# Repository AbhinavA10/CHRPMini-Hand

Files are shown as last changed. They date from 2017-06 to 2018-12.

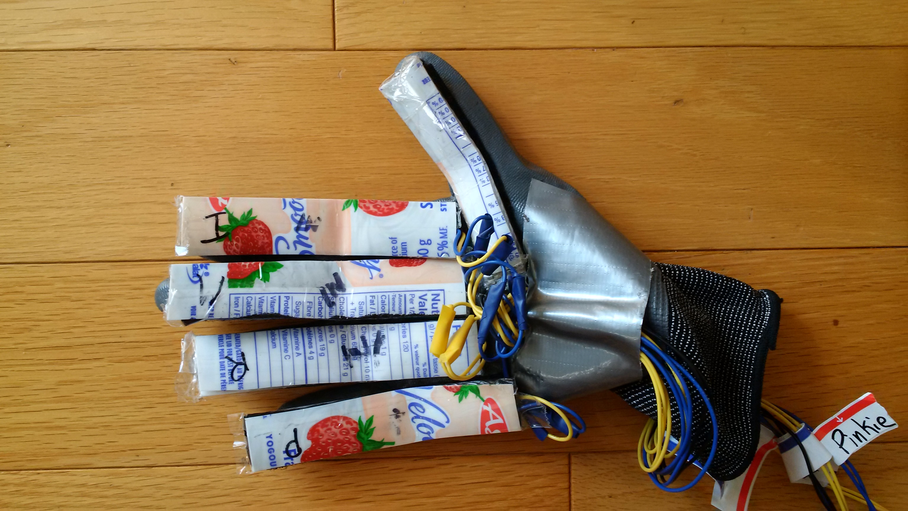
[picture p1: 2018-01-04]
images/Glove.jpg

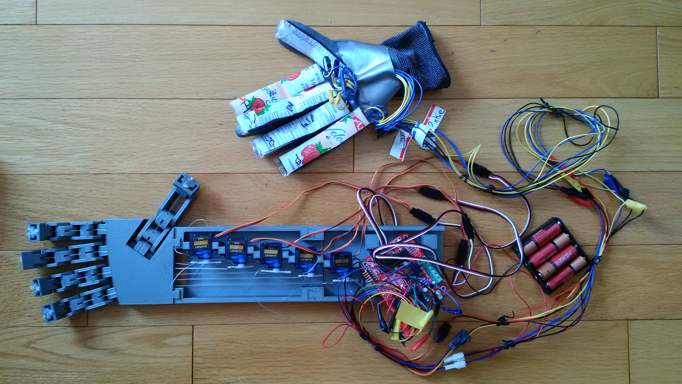
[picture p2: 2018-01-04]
images/Total.jpg

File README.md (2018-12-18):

# CHRPMini-Hand

This is the repo for a flex-controlled 3D printed robotic hand that I made as my summative, in grade 11 for Computer Engineering.
The technical report of this project can be found [here](docs/Technical_Report.pdf)

Demonstrations of the hand are available [here](videos)
Images of the hand can be found [here](images)

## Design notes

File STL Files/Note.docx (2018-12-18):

Measurements / Designs are in millimeters.

Base → Base of the finger (proximal phalanx)

Middle → Middle of the finger (intermediate phalanx)

Top → last joint of the finger (distal phalanx)

Cover → end part of the distal phalanx (fingertip)

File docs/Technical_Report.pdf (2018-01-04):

# Servo Controlled Robotic Hand with Flex Sensing

## Abhi Agrahari and Eric Schilla

## June 21

## Abstract

The main goal was to create an animatronic controller for a robotic hand. The user is to wear a glove, that has flex sensors attached (similar to the Nintendo Power Glove). These sensors’ values are processed by the board, and sent to the respective servos in the robotic hand. If the user bends their hand slightly, the robotic hand bends slightly. Thus, the robotic hand mimics the movement of the user’s hand.

## Table of Contents

Abstract
Table | of | Contents
Introduction
Hardware Design
Prototype Versioning of a Finger Palm and Arm Design
Flex Sensors
Software
Servo Timing
Github and MPLAB
Summary
Future Improvements
References
Appendix
GitHub Links:
Graphite-based Flex Sensor Technical Drawings of the Hand Basic Design
Fishing Line Paths
Screw Hole and Servo Dimensions Versions of the Index Finger
Original Design
Version 1 - Fundamental Design Flaw Version 2 and 3 - Joints are too loose Version 4 - Final Version, A Success

## Introduction

Any intermediate programmer that is experienced with hardware, like ourselves, would be able to understand this report. The general technologies involved are servos, and flex sensors.
For our summative, we wanted to create something that combined mechanical/hardware aspects, and programming/software aspects. On YouTube, we had seen videos of creating drones, and others of robotic body parts. After making a drone, we would feel like we have achieved quite a lot as we would have made something that can fly. However, the cost of making a drone would be much greater than buying one, and the store bought one would be better calibrated and suitable for flying. So there really was no point to that. When deciding on a robotic body part, we narrowed down to a couple. We chose to go with a hand because we could print and test many parts to create the needed joints, but also because we could find a way to make it mimic our movements. So overall, design and programming a robotic hand seemed like a good challenge for us.
This report intends to cover the design process behind both the mechanical aspects of the robotic hand, the self-made flex sensors, and the code created for this project.

## Hardware Design

For this project, we designed all hardware related components besides the servos, and the main circuit board. Essentially, we designed the flex sensors that are used, and the 3D printed hand. The 3D printed hand’s joints are controlled by fishing line, and are attached to 5x 9 gram micro servos.

## Prototype Versioning of a Finger

A long amount of time was spent in understanding and resolving the design to be able to have a finger that moves by pulling on two strings. Images of both prototype versions, and final versions can be seen in the appendix.
The versions progressed from not being able to move a finger at all due to a fundamental design flaw, to being able to fully bend all joints. A main difficulty was creating these joints to properly fit into one another. In the end, once a working version was made, we left the joints detachable instead of hooking onto one another as it is easier to create and assemble (see appendix for design).

## Palm and Arm Design

Besides having 5 similar fingers, we needed to also create a palm and an arm that the fingers would attach to. The palm was designed such that each finger’s fishing line had a unique path through the inside of the palm. This ensured that the lines did not cross over or tangle in each other. The arm’s servo supports were then aligned with the holes in the base of the palm so that enough torque could be generated by the 9 gram servos.

## Flex Sensors

Flex sensors are a special type of variable resistor. Their resistance changes as they bend. One side of the sensor is printed with a polymer ink that has conductive particles embedded in it. When the sensor is straight, the particles give the ink a low resistance, and when the sensor is bent away from the ink, the conductive particles move further apart, increasing this resistance. Thus, by combining the flex sensor with a static resistor we could create a voltage divider.
Or at least that was our idea. Originally, a plan was made to purchase 5-7 flex sensors from an online site, and use them. Unfortunately, flex sensors cost much too much (around $7) per sensor, so having just 5 sensors would have cost us around $35.
Various designs were found online to make these flex sensors. The designs had a general theme of using conductive foam, graphite covered paper, conductive thread and neoprene, and velostat. Purchasing conductive foam or velostat would have been very troublesome as no seller ships to Canada. So, many attempts were made to make flex sensors out of paper.
The design was sandwiching a piece of paper coloured with graphite, between two pieces of aluminum-taped cardboard. As expected, these did not work very well. Each sensor had large variations in the resistance it gave (~5kΩ), and each sensor by itself did not give consistent results.
Our next design was to sandwich conductive foam instead of paper. This worked much better, and all sensors give a reading of unbent → above 2.2kΩ and fully bent → below 300Ω. We then changed the sandwiching material to strips of yogurt boxes (plastic) instead of cardboard, so that the foam is bent more evenly, allowing greater sensitivity.
To create a voltage divider in this scenario that would give the maximum range for an input signal, we needed a static resistor of the average of 300Ω and 2.2kΩ. This would be a 1.25kΩ resistor. Fortunately, we had access to a 1.37kΩ resistor, which is close enough for our purposes.
Since we used the CHRPMini board, we created the voltage dividers by connecting the 1.37kΩ resistor to each PORTA 5V and PORTA signal pins. The flex sensor was then connected to the signal and the ground pin.

## Software

## Servo Timing

One thing we learned, is that each type of servo has a different timing. For example, the specifications sheet states that a 1ms pulse is -90°, and a 2ms pulse is +90°. However, after some trial and error, it was found that a 540µs pulse is -90°, and a 2.2ms pulse is +90°.

It was pointed out that Servo code isn’t necessarily exact, and can be fudged around a bit. However, we wanted to use the closest possible values. As such, in our code, we do some math to find the value to delay by so that the servos are pulsed every 20ms (see Hand.C in the CHRPMini-Hand repository on Github).

## Github and MPLAB

Getting github to work with MPLAB was difficult at some stages. We were not aware of how to properly integrate the two. Links to our githubs are available in the appendix.

## Summary

Overall, this project was very successful. The 9 gram micro servos were able to create enough torque and pull the fingers closed, and open them again, continuously. The conductive foam flex sensors also had enough variation in the resistance that the servos were able to move to different positions depending on the extremity of the bend. It is astounding that one is able to make flex sensors that cost at least $8, out of some conductive foam that is lying around from other products.
Some ideas this hand could be scaled to create are prosthetics, or a robotic extension for hazardous situations where having a human is not ideal.

## Future Improvements

A recommendation for the future is to buy flex sensors instead of making them ourselves. This would allow us to get more reliable and consistent results. Although making our own sensors using conductive foam was undoubtedly cool, buying them would also bring a greater level of professionalism.
Another future improvement is one that is software related. Currently the thumb is known as “zero” and the pinkie as “four”. We could write code to map finger numbers to more natural values (e.g., Thumb is “one” and Pinkie is “five”). Another code improvement would be to calibrate the flex sensors. This is currently a work in progress. The best way to do it would be to have a 10 second startup period where the user flexes the sensors repeatedly. The program would then determine the lowest resistance/value that each individual flex sensor has. That value would then be mapped to position 255 on the servo. This way, each flex sensor is able to fully bend it’s respective robotic hand piece, regardless of the slight difference in sensors.

## References

Below are websites and pdfs that we referenced while creating this project.

PIC18F25K50 Datasheet (http://ww1.microchip.com/downloads/en/DeviceDoc/30684A.pdf)
SG90 9gram MicroServo Datasheet (http://www.micropik.com/PDF/SG90Servo.pdf)
Learning Fusion 360 (http://help.autodesk.com/view/fusion360/ENU/)
About Flex sensors (https://learn.sparkfun.com/tutorials/flex-sensor-hookup-guide)
Paper Flex Sensors (https://www.youtube.com/watch?v=b7zT94WV-Ek)
Determining Size of array in C (https://stackoverflow.com/questions/37538/how-do-i-determine-the-size-of-my-array-in-c)

## Appendix

## GitHub Links:

https://github.com/AbhinavA10https://github.com/EricSchilha

## Graphite-based Flex Sensor

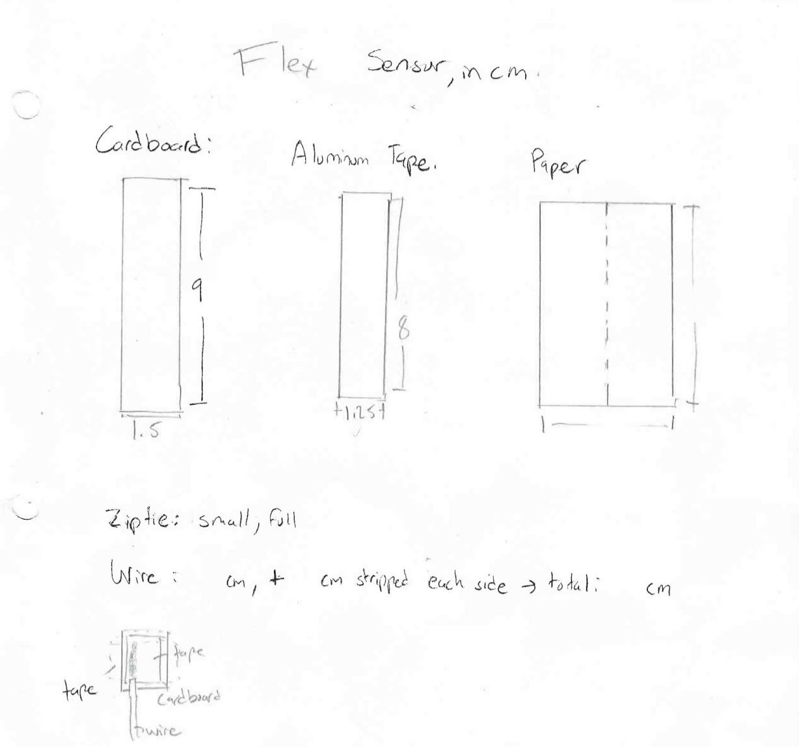
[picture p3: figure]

## Technical Drawings of the Hand

### Basic Design

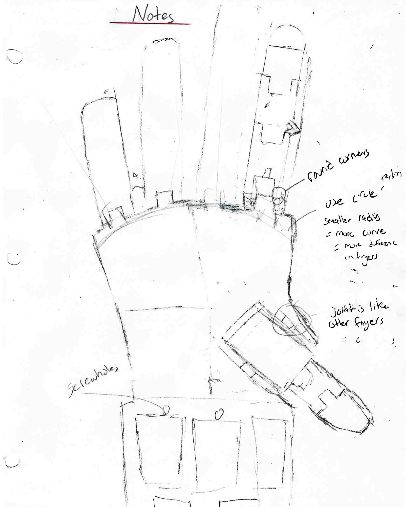
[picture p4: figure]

### Fishing Line Paths

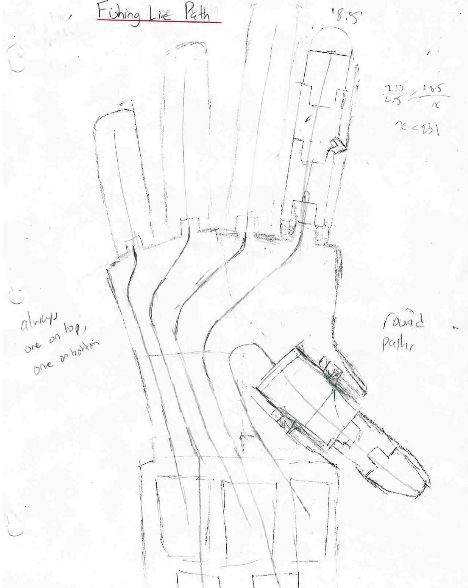
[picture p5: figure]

### Screw Hole and Servo Dimensions

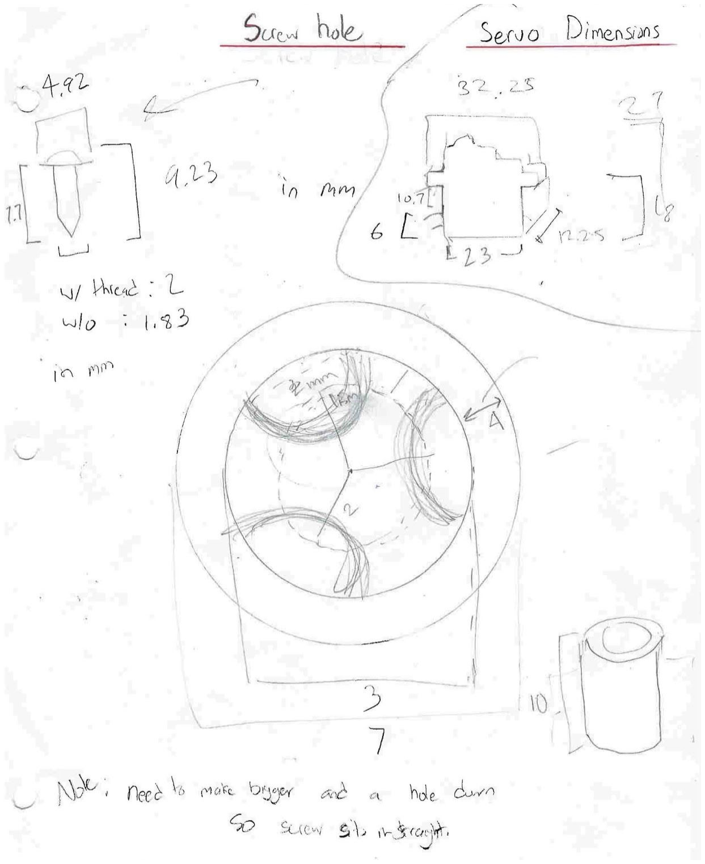
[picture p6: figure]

## Versions of the Index Finger

### Original Design

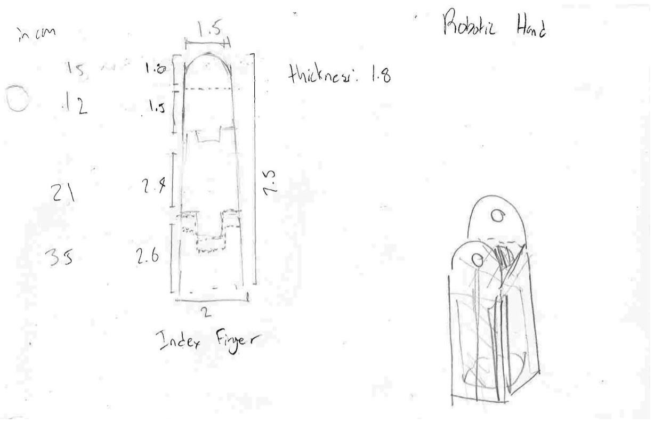
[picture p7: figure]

### Version 1 - Fundamental Design Flaw

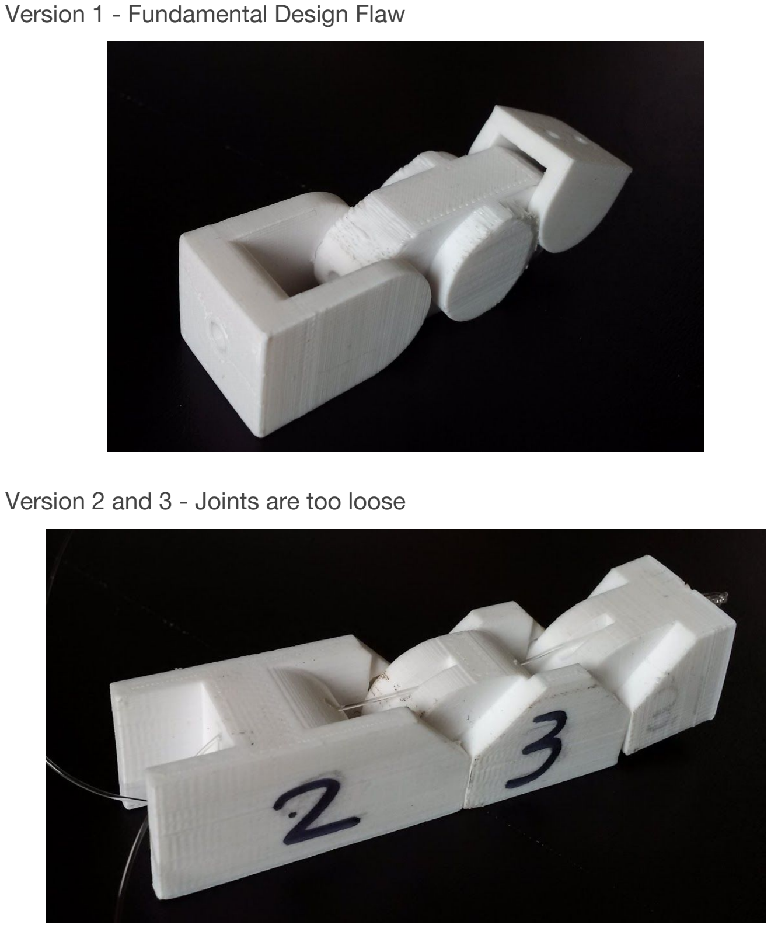
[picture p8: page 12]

### Version 2 and 3 - Joints are too loose

### Version 4 - Final Version, A Success

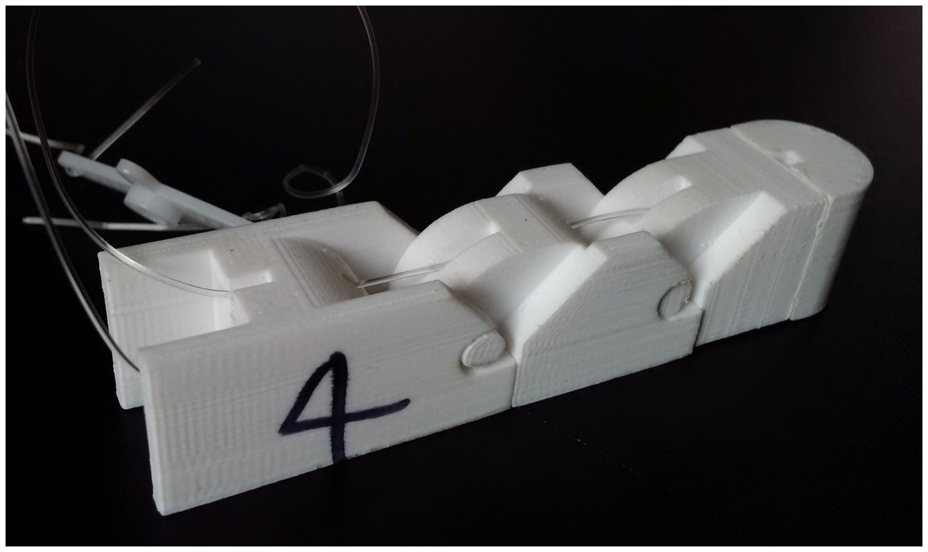
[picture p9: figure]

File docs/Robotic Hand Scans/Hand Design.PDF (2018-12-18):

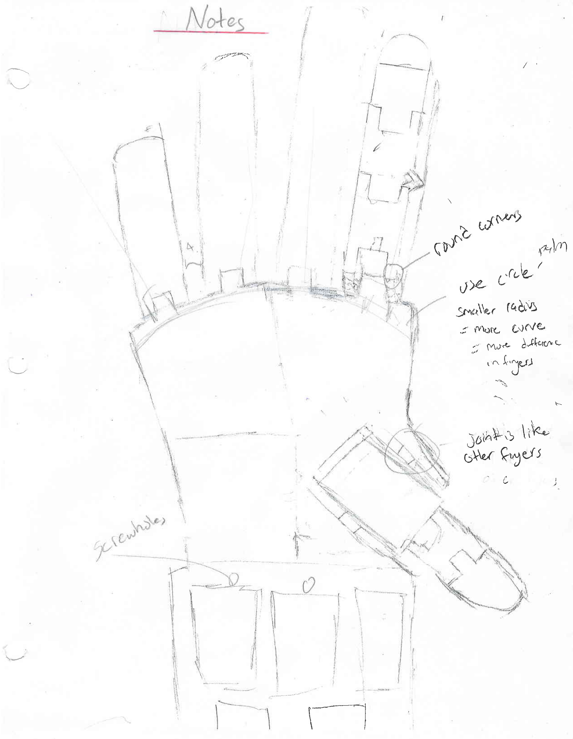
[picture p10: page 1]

\ L,/$r /
( Nf* | sa\nt

t/

## , 'fuw r\.? L

## -hr.,\-*.r t4b'U

# .1 rv\rtc CafVA

| 1.A,)& A"c[ca,r c

,.,. {-.^le,r1
d
.\

!. t .\r,

# \ointr') \ (1\4'

^

a.

### 65$re,f ktqU J

Ll
"Lr

| --4--+l 1t tltt

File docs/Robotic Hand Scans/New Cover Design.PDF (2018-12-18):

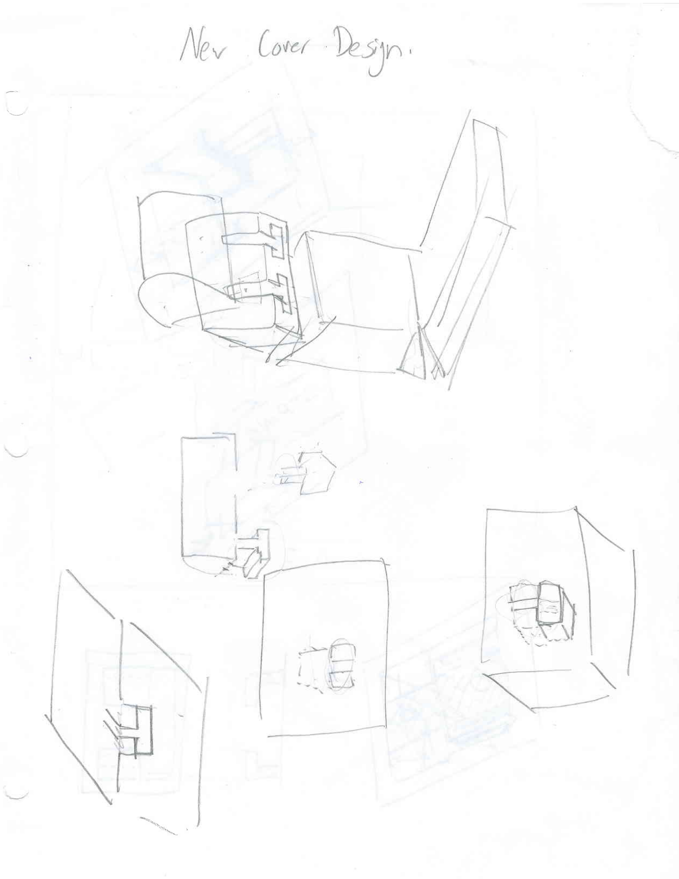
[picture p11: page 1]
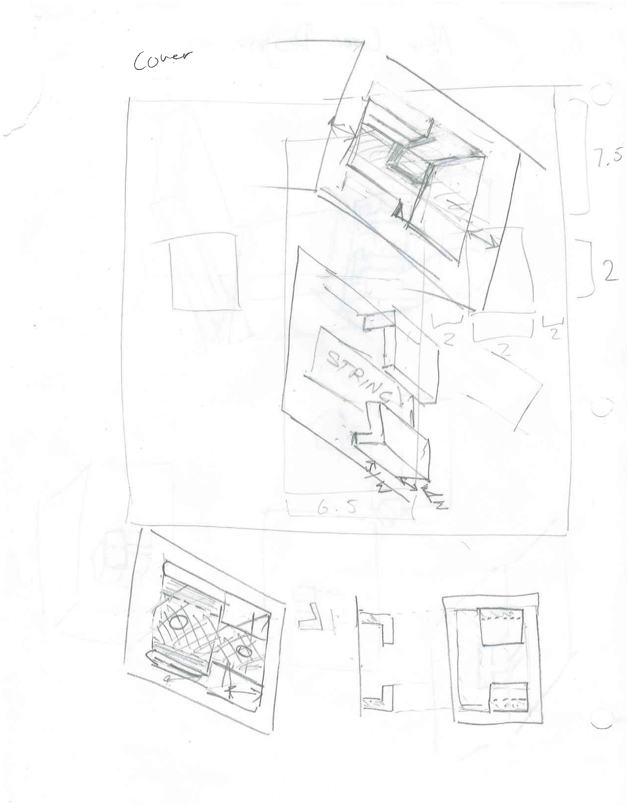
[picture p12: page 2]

Cc:@

{

a\L

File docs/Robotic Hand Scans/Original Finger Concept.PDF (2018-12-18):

'lf

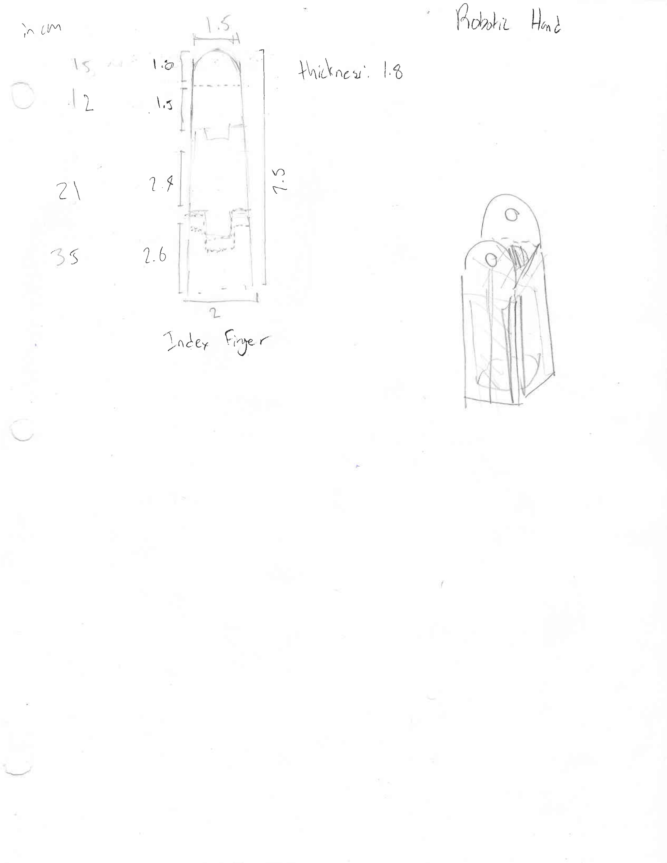
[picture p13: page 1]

frd,rl,z l-1,^J

\"a

\<rtJ

'/6

)^ t inn
lWt\ ^er' I t

)-

\n
Z\ | tr-
'5

'-)nJey €;'yr ,

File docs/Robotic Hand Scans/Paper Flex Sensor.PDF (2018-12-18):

### Ar r

## (urJb*".r&:

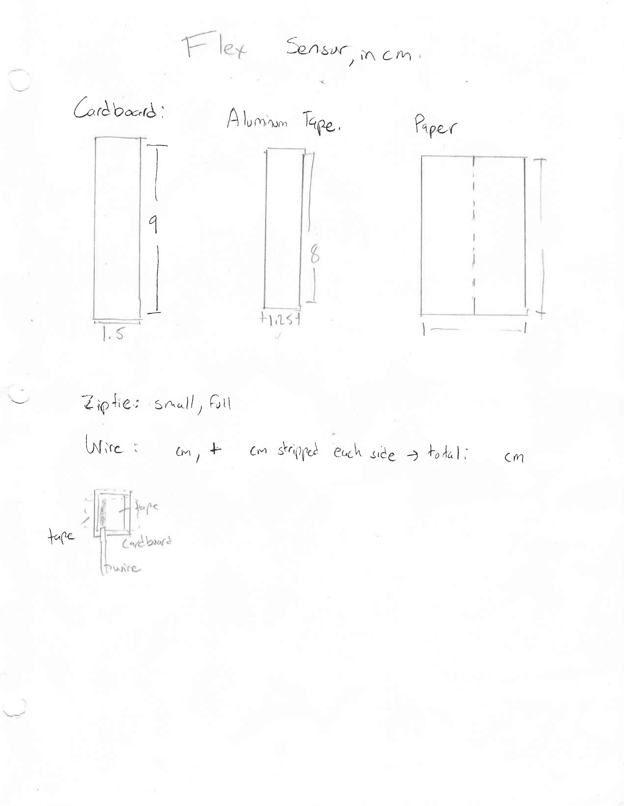
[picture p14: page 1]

-En &)( V\ C n1 / "' '

/-l le r^r1no- ,QW
, | ?n ge-r

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
## Zlqiie, S n.".1/ , f,' L\

I
&, I [,N1. . | + | {r*r sk.it){nd C,,c[. s,Ce ) f, Ja I '
CN

l.e

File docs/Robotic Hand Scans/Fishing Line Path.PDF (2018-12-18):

ir i;

f. i:

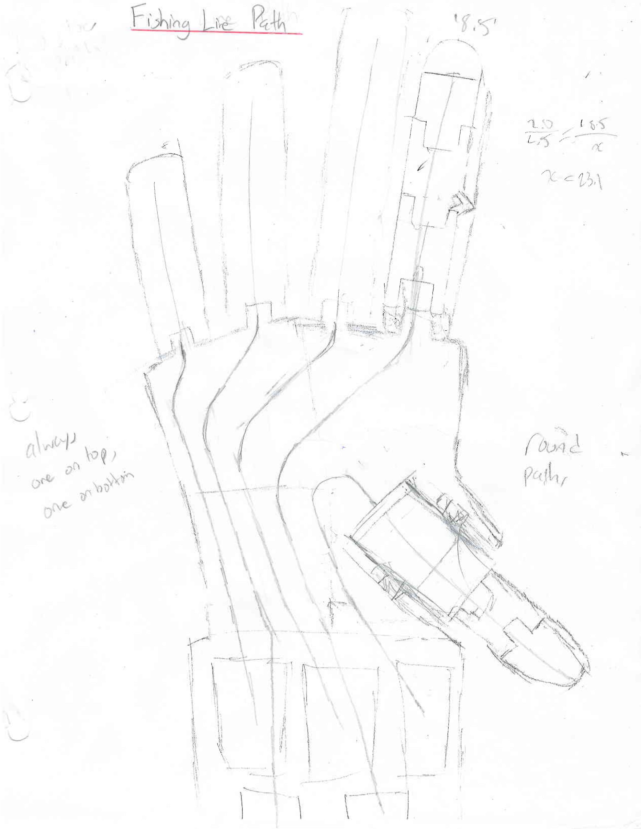
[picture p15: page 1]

/i

I
I

,-\

I
\

## 1: tllr

ll

.'l

# jrt M

t. \,
| ,fr
t::ii /, | i
| 'rl
| 'i

i
,i

),

1r
l\.

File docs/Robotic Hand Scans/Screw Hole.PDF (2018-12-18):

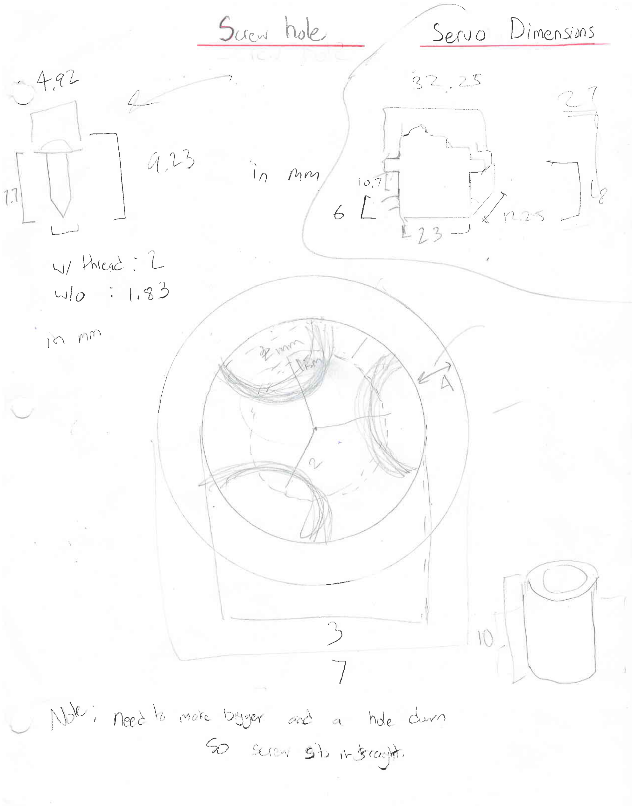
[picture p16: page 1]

ll!-\t- {f1*r ILOVr

.\
)eru o Du*nurnt

() ' .,) )-'

,,/ t

i4 l
*3.L | /

a
L*-
i | 'f 'L
,'( ,'- )
r\wl I o,'7
I
{r L- r)

l\ \ - l
\/ Xtrtc'td L-
| | - , -.'J, t-l/O | t,*b-v

.. ',-r)
1 c-t I', I'

..\. \\;\t', il^lef r \' {,}:,i( lrlJ,r .,,,,i} , hdp ()-,v,n

(sO i.t i ,, ,,,, g'\ , rr.$ r;.r,,-,,f, ,

I
I

-t

I
I
I

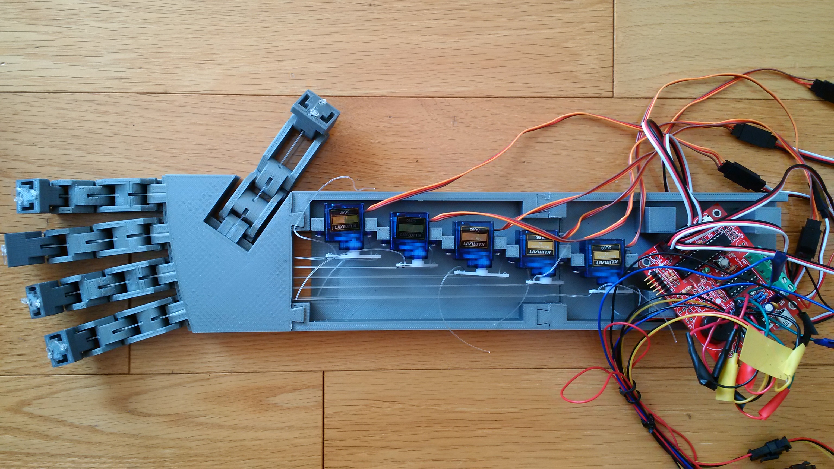
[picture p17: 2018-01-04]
images/Hand.jpg

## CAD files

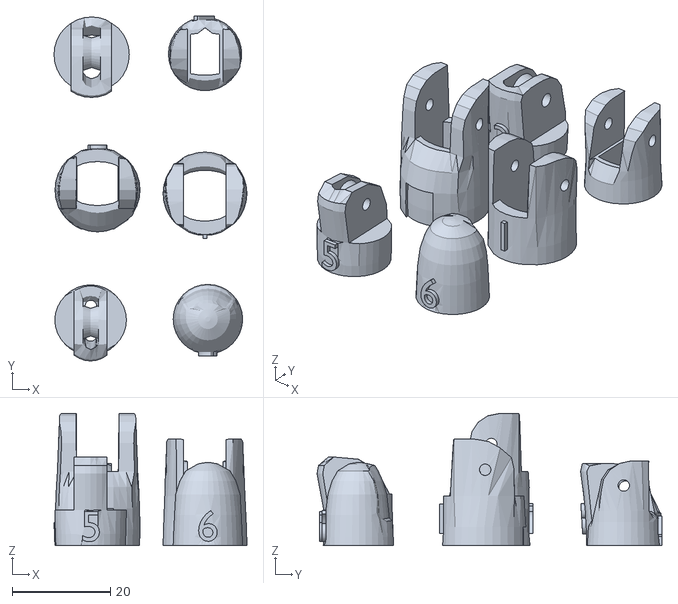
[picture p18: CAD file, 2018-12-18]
docs/Sources/InMoov_Finger_Starter/FingerIndexV2.stl
39.4 x 70.4 x 27.0

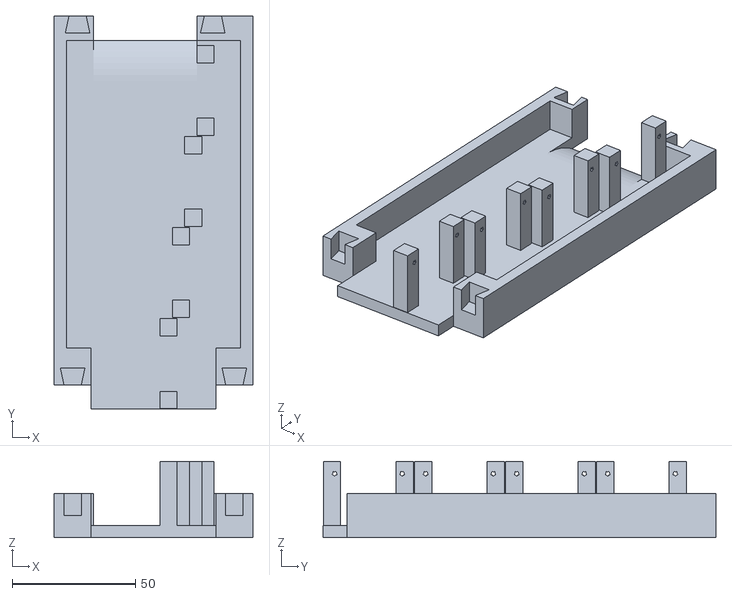
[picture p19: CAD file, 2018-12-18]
STL Files/Arm - June 16/arm pt1.stl
80.7 x 159.7 x 31.0

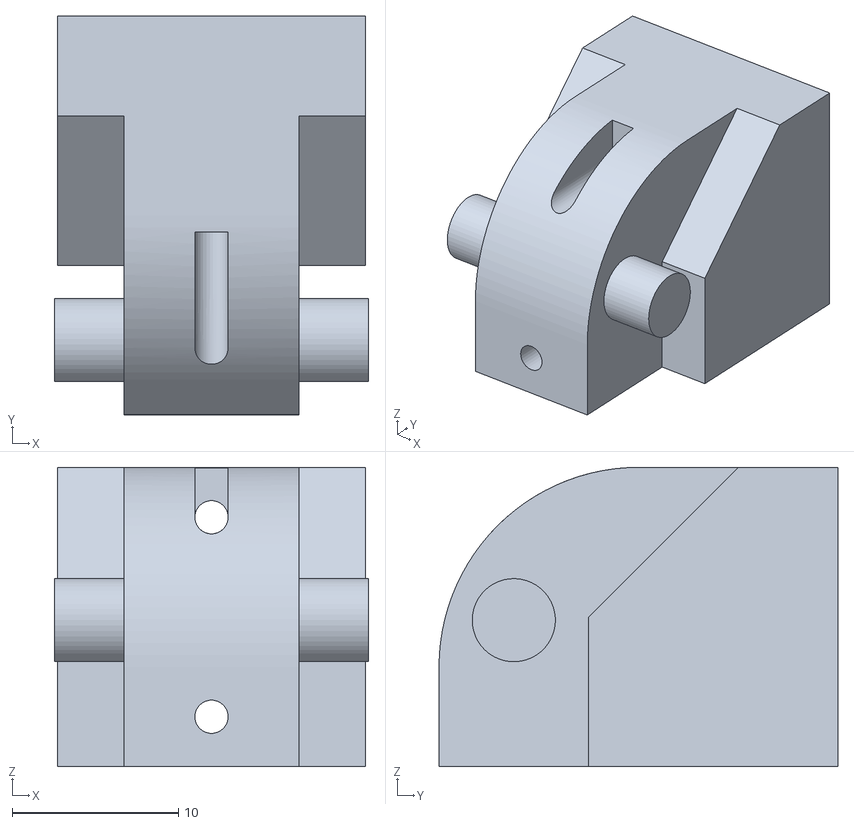
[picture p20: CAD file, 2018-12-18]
STL Files/Failed Versions/Index Finger V4-1/top V4-1.stl
18.9 x 24.0 x 18.0

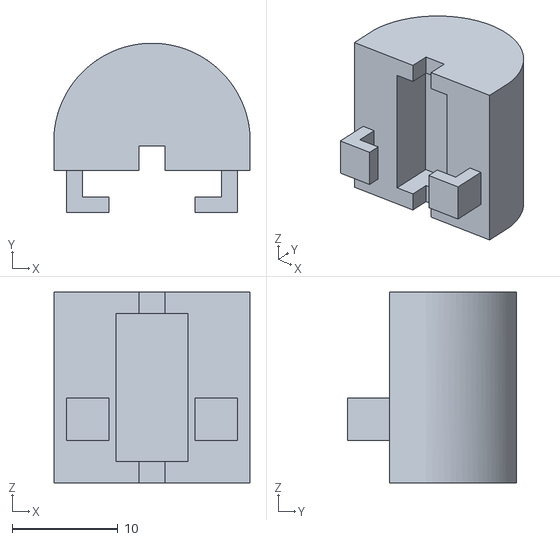
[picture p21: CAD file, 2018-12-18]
STL Files/Failed Versions/Index Finger V4-2/cover V4-2.stl
18.5 x 16.0 x 18.0

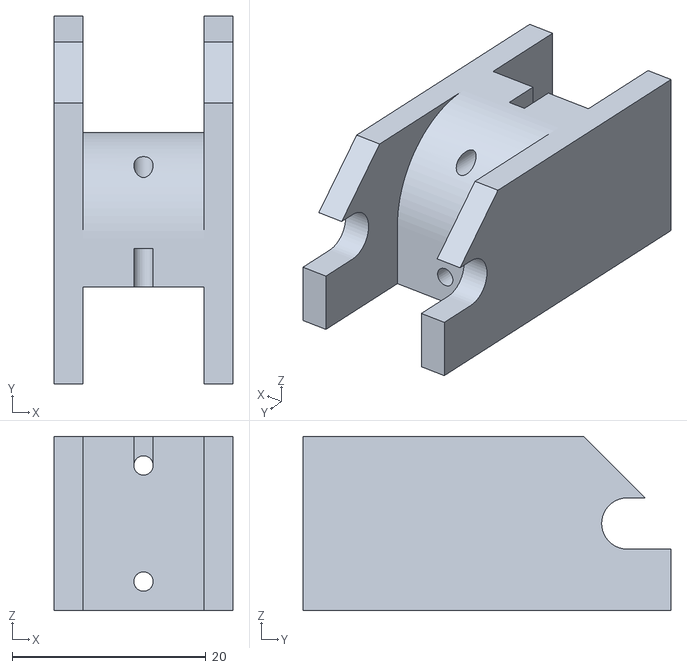
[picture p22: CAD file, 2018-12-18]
STL Files/Failed Versions/Index Finger V4/base V4.stl
18.5 x 38.0 x 18.0

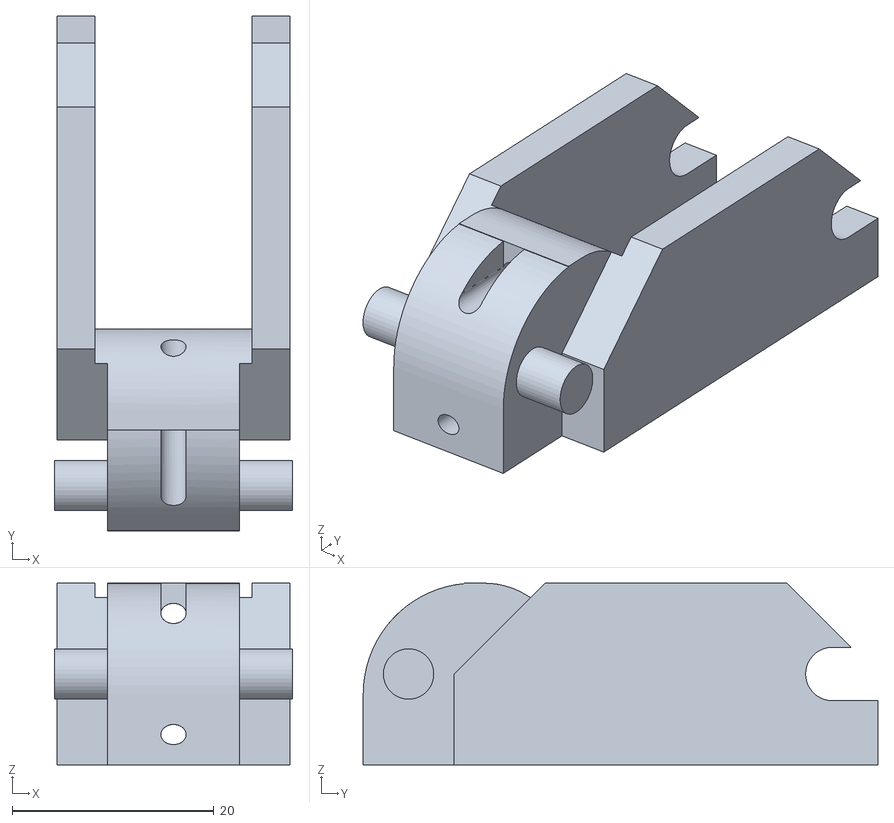
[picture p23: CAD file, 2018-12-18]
STL Files/Palm and more urgent trials - June 15/Thumb Mid Updated.stl
23.6 x 51.0 x 18.0

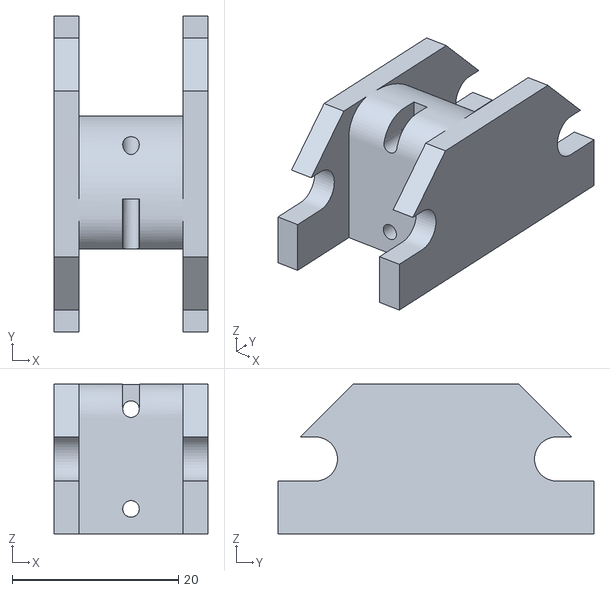
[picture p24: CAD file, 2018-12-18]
STL Files/Parts and Fingers - June 12/Index Base x2.stl
18.5 x 38.0 x 18.0

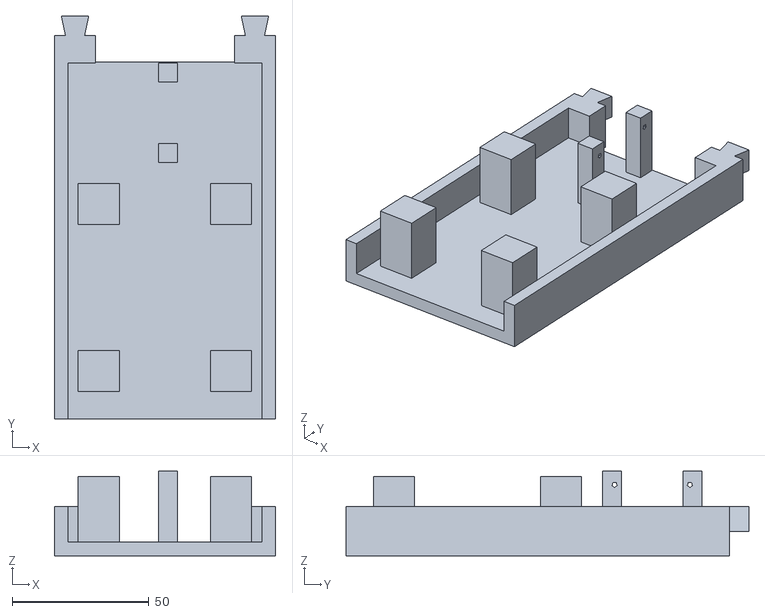
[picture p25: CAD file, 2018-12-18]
STL Files/Arm - June 16/arm pt2.stl
80.7 x 147.0 x 31.0

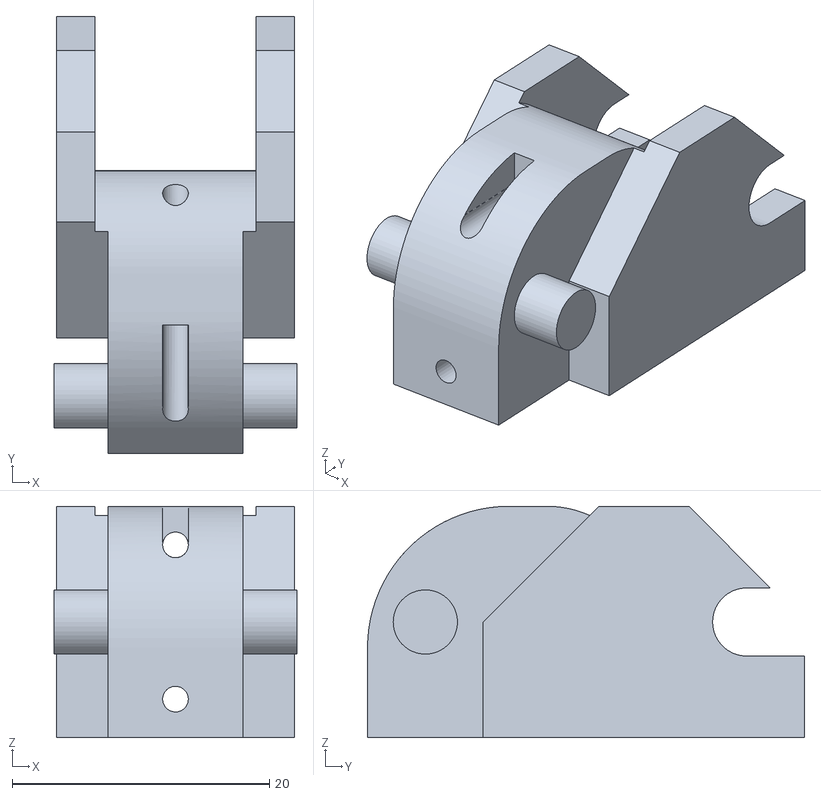
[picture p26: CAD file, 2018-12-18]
STL Files/Failed Versions/Index Finger V4/middle V4.stl
18.9 x 34.0 x 18.0

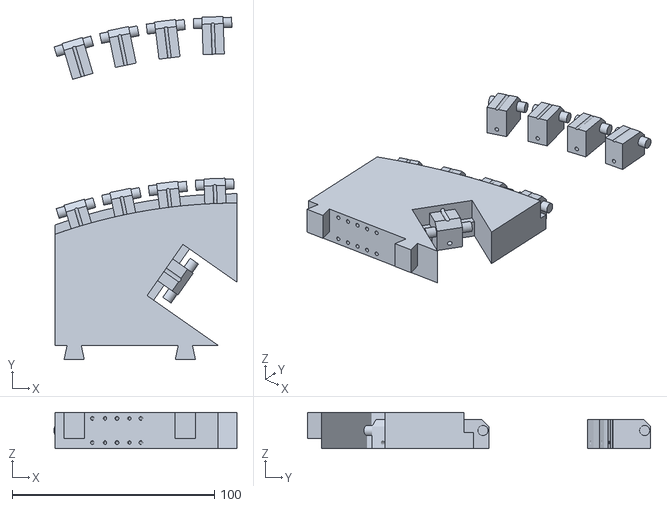
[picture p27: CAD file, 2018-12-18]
STL Files/Palm and more urgent trials - June 15/palm web download.stl
90.4 x 169.7 x 18.0

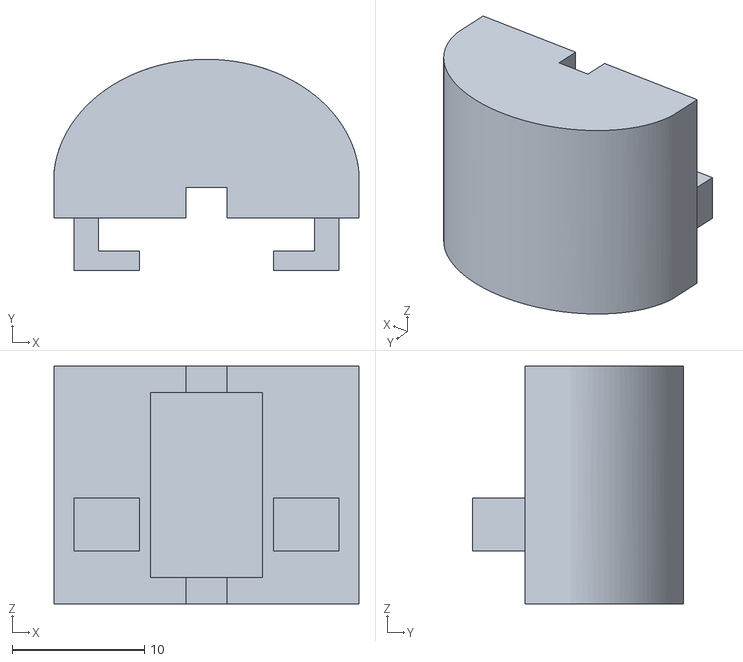
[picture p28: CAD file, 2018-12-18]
STL Files/Parts and Fingers - June 12/Thumb Cover.stl
23.1 x 16.0 x 18.0

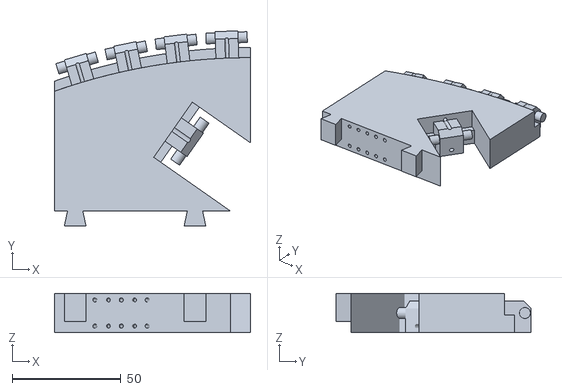
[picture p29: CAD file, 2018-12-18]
STL Files/Palm and more urgent trials - June 15/palm medium binary.stl
90.0 x 89.7 x 18.0

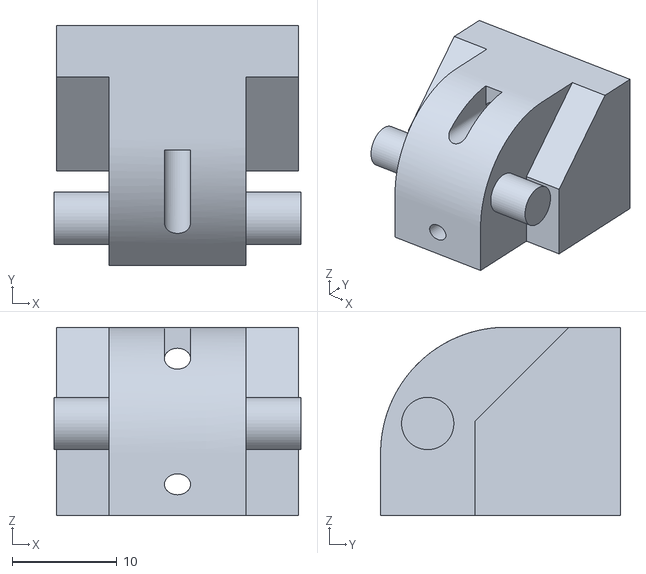
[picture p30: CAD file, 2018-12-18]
STL Files/Parts and Fingers - June 12/Thumb Top.stl
23.6 x 22.9 x 18.0

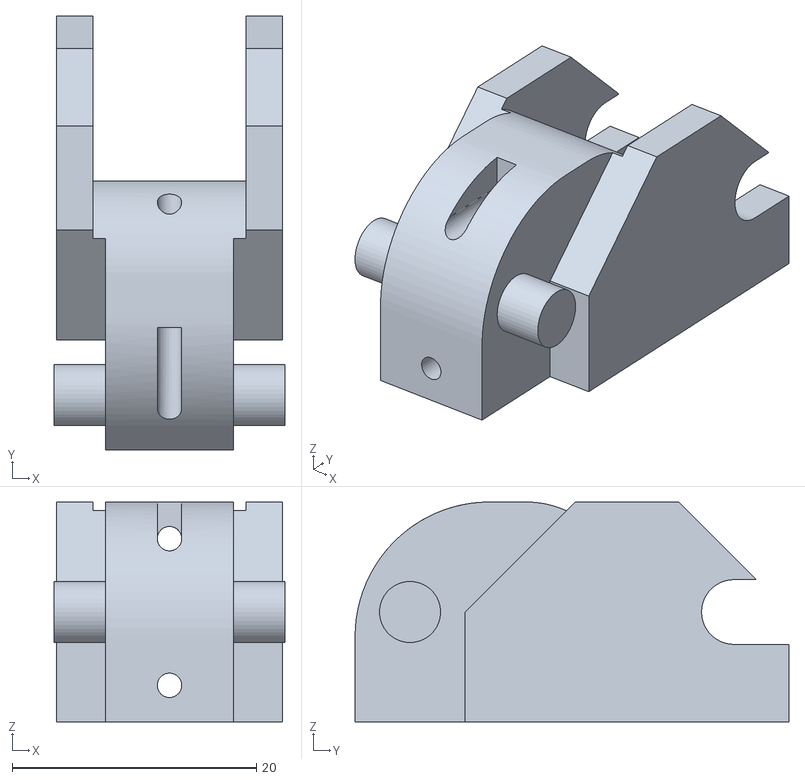
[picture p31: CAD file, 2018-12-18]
STL Files/Parts and Fingers - June 12/Middle Mid.stl
18.9 x 35.5 x 18.0

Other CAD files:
dist/default/production/CHRPMini-Hand.production.obj
STL Files/Failed Versions/Index Finger V4-1/cover V4-1.stl
STL Files/Failed Versions/Index Finger V4-2/top V4-2.stl
STL Files/Parts and Fingers - June 12/Thumb Mid.stl
STL Files/Failed Versions/Index Finger V1/Index Finger Base.stl
STL Files/Failed Versions/Index Finger V1/Index Finger Middle.stl
STL Files/Failed Versions/Index Finger V1/Index Finger Tippy Top.stl
STL Files/Failed Versions/Index Finger V1/Index Finger Top.stl
STL Files/Failed Versions/Index Finger V2/base.stl
STL Files/Failed Versions/Index Finger V2/cover.stl
STL Files/Failed Versions/Index Finger V2/middle.stl
STL Files/Failed Versions/Index Finger V2/top adjusted.stl
STL Files/Failed Versions/Index Finger V2/top.stl
STL Files/Failed Versions/Index Finger V3-1/base V3-1.stl
STL Files/Failed Versions/Index Finger V3-1/cover V3-1.stl
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

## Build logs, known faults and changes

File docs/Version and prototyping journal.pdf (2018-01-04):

Index | Finger | Prototyping | Journal

We had first built an index finger, and needed to test it. Getting the right amount of torque and having it actually function is what took the most time. This document is a journal of each different version of the finger, and the journey to get it to work.

### Version 1:

Flaws:
- Single hole provides no force to turn.
- Top phalanx was not designed with the intent to move in mind.

### Version 2:

Updates:
- Made 2 holes instead.
- Reworked from scratch

Flaws:
- Joints are much too loose. Middle phalanx wiggles all over the place.

### Version 3:

Updates:
- Adjusted fishing line hole for better torque - May 8
- Adjusted length of some pieces - May 8
- Adjusted extrusions so they don’t wiggle.

Flaws:
- Joint pokey things are much too out now. Had to file down from 16.5mm to 15.9mm

### Version 3.1:

Updates:
- Reduced joints’ extrusion by 0.3mm each

- Added top down type cut in top hole in the base.
- Adjusted top cover extrusions
- Pulling on the string to turn works on all joints now

Flaws:

- Top phalanx still has trouble fitting in. Need to redesign joints
- Top joint also is offset up? And seems to get stuck
- Top phalanx doesn’t want to put a support when printing?

### Version 4:

Updates:
- Remodelled joint → new design, to test
- Remodelled top cover joint

Flaws:
- Top cover joint doesn’t fit. Had to file down

### Version 4-1:

### Version 4-2:

Updates:
- Fixed top cover dimensions
- Adjusted hole width by 0.3mm (inwards)
- Adjusted other parts of hole by various amounts

Flaws:
- Seem to be none.

## NOTES

When getting ready to print:
1. Create a separate copy for each component/piece
2. Remove all other components
3. Join all bodies.
4. Download from Web - as STL

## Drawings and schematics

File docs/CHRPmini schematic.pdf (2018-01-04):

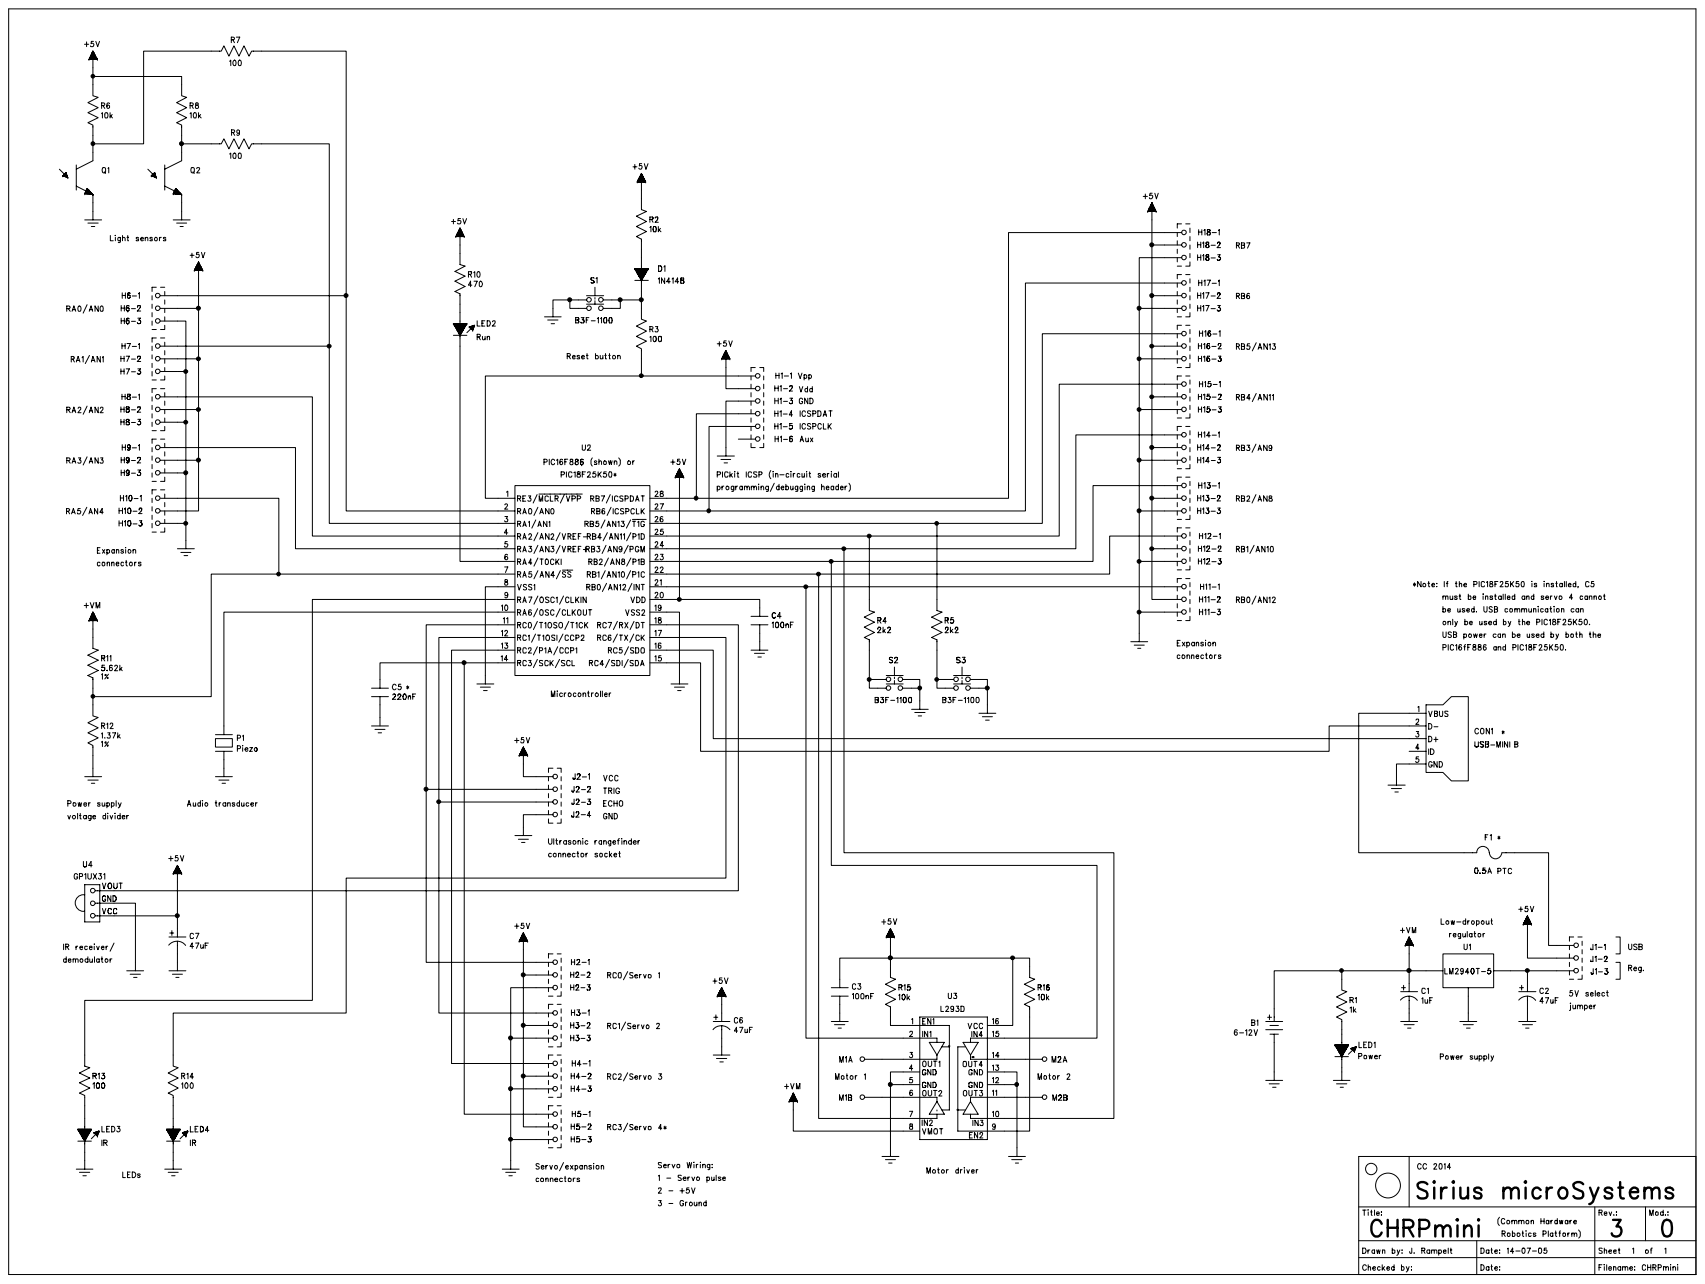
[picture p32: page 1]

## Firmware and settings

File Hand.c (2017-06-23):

/*==============================================================================
    Project: Hand
    Version: 3.1				Date: May 29, 2017
    Target: CHRPMini			Processor: PIC18F25K50
==============================================================================*/
// fix mode 0 bug
// fix calibration
#include    "xc.h"              // XC compiler general include file
#include    "stdint.h"          // Include integer definitions
#include    "stdbool.h"         // Include Boolean (true/false) definitions
#include    "CHRPMini.h"        // Include CHRPMini constant symbols and functions

// Have set linker ROM ranges to 'default,-0-1FFF,-2006-2007,-2016-2017' under "Memory model" pull-down.
// Have set linker Code offset to '0x2000' under "Additional options" pull-down.

/*==============================================================================
    Finger Pathing
==============================================================================*/
#define THUMB           0	// Port B value for both motors stopped
#define INDEX           1
#define MIDDLE          2
#define RING            3
#define PINKIE          4

/*==============================================================================
    VARIABLES
==============================================================================*/
unsigned char arcPos[5], arcMaxBendPos[5] = {255, 255, 255, 255, 255}; //Position for each finger. 0 represents open. 255 means fully closed.
unsigned char cMode, cDelay, cGesture, cCountFingerCycle, cCycleIncrement;
//cMode is the mode the hand is in. i.e, decides what the hand will do
//cDelay is for counting duration when mode select button is held 
//cGesture is for the command number
//cCountFingerCycle and cCycleIncrement are used in creating the "come here" gesture
bool modeSelect, isPressedForMode, isPressedForGesture, buttonWasLetGo, calibMode;
// the above variables are needed to properly navigate mode selection, calibration, and gesture cycling
int nDelay, nCalibrationCounter;
//nDelay is for keeping track of the proper delay to pulse servos every 20ms
//nCalibrationCounter is for having the calibration mode on for only 10 seconds/beeps.

/*==============================================================================
    SET POS
        Function to individually set position of each servo to the passed value.
        We are not able to set an entire array to different values, once it is initialized.
        So to avoid recreating the array, or importing <algorithm> this function
        was made to change the position to hard-coded values.
        This will allow us to have certain gestures on command.
==============================================================================*/
void setPos(unsigned char a, unsigned char b, unsigned char c, unsigned char d, unsigned char e) {
    arcPos[THUMB] = a;
    arcPos[INDEX] = b;
    arcPos[MIDDLE] = c;
    arcPos[RING] = d;
    arcPos[PINKIE] = e;
}

/*==============================================================================
    BEEP
        A generic beep function. Used in other parts of the code so that 
        we can tell what mode it is in.
==============================================================================*/
void beep(unsigned int pitch, unsigned int duration) {
    for (duration; duration != 0; duration--) {
        BEEPER = !BEEPER;
        for (unsigned int j = pitch; j != 0; j--);
    }
}

/*==============================================================================
    INIT VARIABLES
        A function to set starting values for each variable.
        Created so that setting starting values is made simple as it is all in 
        one spot and not when they are created
==============================================================================*/
void initVariables() {
    setPos(0, 0, 0, 0, 0); // starting position of servos is an open hand.
    modeSelect = false;
    isPressedForMode = false;
    isPressedForGesture = false;
    buttonWasLetGo = true;
    calibMode = false;
    cMode = 0;
    cDelay = 0;
    cCountFingerCycle = 5;
    cCycleIncrement = 5;
    nCalibrationCounter = 0;
}

/*==============================================================================
    AD CONVERT
        A/D conversion function. Pass the channel to be converted using one of the
        definitions in CHRP3.h. Returns the most significant 8-bits of the result.
==============================================================================*/
unsigned char adConvert(unsigned char chan) {
    ADON = 1; // Turn A-D converter on
    ADCON0 = (ADCON0 & 0b11000011); // Change the conversion channel by wiping
    ADCON0 = (ADCON0 | chan); // CHS bits and ORing with selected channel

    NOP(); // Wait to allow the input to stabilize
    NOP(); // NOPE
    NOP();
    NOP();

    GO = 1; // Start the conversion

    while (GO); // Wait for the conversion to finish

    ADON = 0; // Turn A-D converter off
    return (ADRESH); // Return the upper 8-bits of the result
}

/*==============================================================================
    CHECK MODE 
        Function to check if the mode needs to change
        If S1 is held, go into mode select. Each time S1 is pressed, switch mode.
        Confirm mode, and leave mode select by holding S1 again.
==============================================================================*/
unsigned char checkMode() {
    unsigned char cTempMode = cMode;
    if (S1 == 0) {
        isPressedForMode = true;
        if (!modeSelect && buttonWasLetGo) { // user is holding button to enter mode selection
            cDelay++;
            if (cDelay == 20) {
                cDelay = 0;
                modeSelect = true;
                buttonWasLetGo = false;
                isPressedForMode = false;
                beep(200, 500);
                for (unsigned char i = 0; i < 5; i++) {
                    arcPos[i] = (cTempMode == i) ? 255 : 0; // Bend the finger that is equal to the mode; Straighten all the others.
                }
            }
        } else if (buttonWasLetGo) {
            cDelay++;
            if (cDelay == 20) { // user is holding to leave mode select
                cDelay = 0;
                modeSelect = false;
                buttonWasLetGo = false;
                isPressedForMode = false;
                beep(400, 500);
                //cTempMode--; // to compensate for the cTempMode++ some lines below
                if (cTempMode == 0) {
                    calibMode = true;
                } else {
                    calibMode = false;
                }
                setPos(0, 0, 0, 0, 0); //Straighten all fingers
            }// else { // user has pressed the button to change the mode

            //}
        }
    }

    if (S1 == 1) { // mode is changed after the button is let go. This is done so that the user is able to leave mode select.
        if (buttonWasLetGo && isPressedForMode && modeSelect) {
            cTempMode++;
            if (cTempMode == 5) {
                cTempMode = 0;
            }
            for (unsigned char i = 0; i < 5; i++) {
                arcPos[i] = (cTempMode == i) ? 255 : 0; // Bend the finger that is equal to the mode; Straighten all the others.
            }
        }
        buttonWasLetGo = true;
        cDelay = 0;
        isPressedForMode = false;
    }
    return cTempMode;
}

/*==============================================================================
    PULSE SERVOS 
        Servo function to pulse all 5 servos one after the other.
==============================================================================*/
void pulseServos() {
    /*  Servo specifications
     * The servo turns 180 degrees. Below values were found by trail and error
     * as the datasheet was an approximation
     * 0.54ms to 2.07ms on time, and a 20ms period.
     */

    //Thumb
    SERVOTHUMB = 1; //Turn it on
    __delay_us(540); //540 works well to give a -90 degree pulse.
    for (unsigned char i = 255 - arcPos[THUMB]; i != 0; i--) {
        /*
         * The 255- arcPos[x] is needed so that the servo turns in the opposite 
         * direction i.e., starts at max position
         * This stops the threads in the hand from crossing over each other.
         */
        __delay_us(6); //For the SG90 servo, a 6us delay for each position
        // allows a max pulse of 2.07ms for +90 degrees.
    }
    SERVOTHUMB = 0; //Turn it off

    //Index Finger
    SERVOINDEX = 1;
    __delay_us(540);
    for (unsigned char i = 255 - arcPos[INDEX]; i != 0; i--) {
        __delay_us(6);
    }
    SERVOINDEX = 0;

    //Middle Finger
    SERVOMIDDLE = 1;
    __delay_us(540);
    for (unsigned char i = 255 - arcPos[MIDDLE]; i != 0; i--) {
        __delay_us(6);
    }
    SERVOMIDDLE = 0;

    //Ring Finger
    SERVORING = 1;
    __delay_us(540);
    for (unsigned char i = 255 - arcPos[RING]; i != 0; i--) {
        __delay_us(6);
    }
    SERVORING = 0;

    //Pinkie Finger
    SERVOPINKIE = 1;
    __delay_us(540);
    for (unsigned char i = 255 - arcPos[PINKIE]; i != 0; i--) {
        __delay_us(6);
    }
    SERVOPINKIE = 0;
}

/*==============================================================================
    DELAY
        Delay function to delay by the correct amount of time such that pulses between
        each servo is always 20ms.
        Takes the goal of a 20ms pulse, subtracts guaranteed servo pulses of 0.54ms
        and then also subtracts any extra pulses for each position. (-2500) was 
        added as an approximated adjustment factor to account for clock cycles/delays in 
        other parts of the code.
==============================================================================*/
void delay() {
    nDelay = (int) ((20000 - 2500 - 540 * 5 - arcPos[THUMB] - arcPos[INDEX] - arcPos[MIDDLE] - arcPos[RING] - arcPos[PINKIE]) / 6);
    for (int i = nDelay; i != 0; i--) {
        __delay_us(6);
    }
}

/*==============================================================================
    CONVERT SENSORS
        Function to convert all analog flex sensors to 8bit value by 
        calling the A/D conversion function.
        
        The position must equal 255 minus the value that the A/D conversion returns.
        This is because the conductivity of the foam increases as it is bent, 
        meaning less resistance, and therefore a lower value. Without this, the
        hand would start as a fist, and then unbend as the user bends the glove.
==============================================================================*/
void convertSensors() {
    arcPos[THUMB] = 255 - adConvert(SENSORTHUMB);
    arcPos[INDEX] = 255 - adConvert(SENSORINDEX);
    arcPos[MIDDLE] = 255 - adConvert(SENSORMIDDLE);
    arcPos[RING] = 255 - adConvert(SENSORRING);
    arcPos[PINKIE] = 255 - adConvert(SENSORPINKIE);
}

/*==============================================================================
    CENSOR FINGER
        Function to censor out the middle finger. i.e., can't give someone
        the finger.
==============================================================================*/
void censorFinger() {
    if (!calibMode) {
        unsigned char cMin = 255;
        if (arcPos[MIDDLE] < arcPos[THUMB] && arcPos[MIDDLE] < arcPos[INDEX] && arcPos[MIDDLE] < arcPos[RING] && arcPos[MIDDLE] < arcPos[PINKIE]) {
            // to find the size of array in C, you need to use sizeof(). Instead of
            //that, we just hard-coded in 5 in the line below
            for (unsigned char i = 0; i < 5; i++) {
                if (cMin > arcPos[i] && i != MIDDLE) {
                    cMin = arcPos[i];
                }
            }
            arcPos[MIDDLE] = cMin;
        }
    }
}

/*==============================================================================
    CALIBRATION
        Function to calibrate all analog flex sensors in a period of 10 seconds
        after entering sensor mode (0)
==============================================================================*/

/*
 * SOME INFO:
 * Dividing a 5V signal into 256 states results in an input sensitivity of about 19.5mV
 * This means  the lowest resistance in a sensor probably gives about a "32"
 * We need to create either a look up table (array of 256) or a conversion factor to map the minimum of 
 * 35 to 0 on the servo, and then spread the other sensor values across the servos
 * http://www.ohmslawcalculator.com/voltage-divider-calculator
 */
void calibrate() {
    modeSelect = false; // just to make sure it's not in mode select
    for (unsigned char i = 0; i < 5; i++) {
        if (arcPos[i] < arcMaxBendPos[i] && arcPos[i] > 0) {
            arcMaxBendPos[i] = arcPos[i];
        }
    }
    nCalibrationCounter++;
    __delay_ms(1);
    if (nCalibrationCounter % 1000 == 0 && nCalibrationCounter != 10000) {
        beep(200, 500);
    }
    if (nCalibrationCounter == 10000) {
        nCalibrationCounter = 0;
        calibMode = false;
        beep(400, 2000);
        // write some code here

    }
}

/*==============================================================================
    COMMANDS
        Function to switch between preprogrammed finger positions
        using the button.
==============================================================================*/
void commands() {
    /*
     * We are able to still change the gesture using the same button
     * because entering mode select requires the user to hold the button 
     * for approximately 3 seconds.
     */
    if (S1 == 0 && !modeSelect) {
        isPressedForGesture = true;
    }
    if (S1 == 1 && isPressedForGesture && !modeSelect) { // gesture changes when button is let go
        isPressedForGesture = false;
        cGesture++;
        if (cGesture == 9)cGesture = 0;
        switch (cGesture) {
            case 0:
                setPos(0, 0, 0, 0, 0); // Open hand
                break;
            case 1:
                setPos(255, 255, 255, 255, 255); // Fist
                break;
            case 2:
                setPos(0, 0, 255, 255, 0); // Spider-man
                break;
            case 3:
                setPos(0, 255, 255, 255, 0); // Hang Loose
                break;
            case 4:
                setPos(200, 0, 0, 255, 255); // Peace sign
                break;
            case 5:
                setPos(200, 200, 0, 0, 0); // A-OK
                break;
            case 6:
                setPos(0, 255, 255, 255, 255); // Thumbs Up
                break;
            case 7:
                setPos(255, 0, 255, 255, 255); // Index pointing
                break;
            case 8:
                setPos(255, 0, 255, 255, 0); // Rock On
                break;
            default:
                break;
        }
    }
}

/*==============================================================================
    HEY KID, WANT SOME CANDY?
        Function to lure small children towards the van.
        (SPOILER: Kid doesn't actually get candy. We can't afford that)
 
        Update: This function actually cycles the index finger back and forth.
        This creates the "come here" gesture with your finger. Maybe the kid
        really will get candy.
==============================================================================*/
void heyKidWantSomeCandy() {
    setPos(255, cCountFingerCycle, 255, 255, 255);
    cCountFingerCycle += cCycleIncrement;
    if (cCountFingerCycle == 255 || cCountFingerCycle == 0) {
        cCycleIncrement *= -1;
    }
}

/*==============================================================================
 MAIN PROGRAM CODE.
==============================================================================*/
int main(void) {
    initOsc(); // Initialize oscillator and wait for it to stabilize
    initPorts(); // Initialize CHRPMini I/O and peripherals
    initANA(); // Initialize Port A analog inputs (for Flex sensors)
    initVariables(); // Initialize all variables 
    while (1) {
        if (!modeSelect) {
            switch (cMode) {
                case 0: // matching glove movements
                    convertSensors();
                    //censorFinger();
                    //if (calibMode) calibrate();
                    break;
                case 1: // pre-programmed gestures
                    commands();
                    break;
                case 2:
                    heyKidWantSomeCandy(); // "come here" gesture
                    break;
                default:
                    break;
            }
        }
        if (!calibMode || modeSelect) {
            pulseServos();
            delay();
        }
        cMode = checkMode();
    }
}

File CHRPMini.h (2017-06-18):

/*==============================================================================
    CHRP 3.1 (PIC18F25K50) symbolic constant definitions.
==============================================================================*/

// TODO - Add other user constant definitions for CHRP3 hardware here.

// Inputs read the Port registers (eg. RC0). Outputs write to the port latches
// (eg. LATC0). Create different symbolic names for pins that will be both
// inputs and outputs using the appropriate PORT and LAT pin names.

// PORTA I/O device definitions

#define	Q1			PORTAbits.RA0		// Phototransistor Q1 input  - 
#define	Q2			PORTAbits.RA1		// Phototransistor Q2 input  - 
#define	VR1			PORTAbits.RA2		// Potentiometer VR1 input   - 
#define	T1			PORTAbits.RA3		// Temperature sensor T1 input
#define	LED2		LATAbits.LATA4		// Run LED, LED2 output
#define	RUNLED      LATAbits.LATA4		// Run LED, LED2 output
#define	VM			PORTAbits.RA5		// Motor supply voltage divider input
#define	BEEPER		LATAbits.LATA6		// Piezo beeper P1 output
#define	P1			LATAbits.LATA6		// Piezo beeper P1 output
#define	LED12		LATAbits.LATA7		// Floor/phototransistor LED (LED12) output

// PORTB I/O device definitions

//#define LED10		LATBbits.LATB0		// LED10 output (LSB)
#define M1A			LATBbits.LATB0		// Motor 1 A output
#define M1B			LATBbits.LATB1		// Motor 1 B output
#define M2A			LATBbits.LATB2		// Motor 2 A output
#define M2B			LATBbits.LATB3		// Motor 2 B output

#define H18         PORTBbits.RB7       // External I/O header H18 input 
#define SERVOTHUMB  LATBbits.LATB7      // Servo 1 output (external header H18)
#define H17         PORTBbits.RB6       // External I/O header H17 input 
#define SERVOINDEX  LATBbits.LATB6      // Servo 1 output (external header H17)
#define H16         PORTBbits.RB5       // External I/O header H16 input 
#define SERVOMIDDLE LATBbits.LATB5      // Servo 1 output (external header H16)
#define H15         PORTBbits.RB4       // External I/O header H15 input 
#define SERVORING   LATBbits.LATB4      // Servo 1 output (external header H15)
#define H13         PORTBbits.RB2       // External I/O header H13 input 
#define SERVOPINKIE LATBbits.LATB2      // Servo 1 output (external header H13)


// PORTC I/O device definitions

#define LED11		LATCbits.LATC6		// Communication/sensor LED, LED11 output
#define IR			PORTCbits.RC7		// IR demodulator U5 input
#define U5			PORTCbits.RC7		// IR demodulator U5 input

// PORTE input pin definition

#define	S1			PORTEbits.RE3		// Switch S1 input

// Analogue-digital converter input channel definitions

#define SENSORTHUMB     0b00000000		// Flex Sensor A-D input channel (Ch0) on AN0/RA0
#define SENSORINDEX     0b00000100		// Flex Sensor A-D input channel (Ch1) on AN1/RA1
#define SENSORMIDDLE    0b00001000		// Flex Sensor A-D input channel (Ch2) on AN2/RA2
#define SENSORRING      0b00001100		// Flex Sensor A-D input channel (Ch3) on AN3/RA3
#define SENSORPINKIE    0b00010000		// Flex Sensor A-D input channel (Ch4) on AN4/RA5

#define	ADVM		0b00010000		// Motor voltage divider A-D input channel (Ch4)
#define ADTD		0b01110000		// PICmicro on-die temperature diode

// Clock frequency for delay macros and simulation

#define _XTAL_FREQ	48000000		// Processor clock frequency for time delays

// TODO - Add function prototypes for all functions in CHRP3.c here.

void initOsc(void); // Oscillator initialization function prototype.
void initPorts(void); // Port initialization function prototype.
void initANA(void); // Analogue PORTA initialization function.

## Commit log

2017-06-21 completed flex sensors
    [CHRPMini-Hand.X.production.obj, CHRPMini-Hand.production.obj]
2018-12-18 Organized images and videos of RoboticHand
    [FingerIndexV2.stl]
2018-12-18 Added STL Files
    [Cover x4.stl, Index Base x2.stl, Index Finger Base.stl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]
